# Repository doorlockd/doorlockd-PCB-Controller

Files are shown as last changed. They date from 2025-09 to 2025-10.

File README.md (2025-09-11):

# Doorlockd controller
This repository contains a PCB for a doorlockd controller, which
(together with a remote card reader) reads RFID tags and controls a lock
solenoid or other devices.

The main controller can be a Rock Pi S or Milk-V Duo S Linux board, which is
stacked on top of this PCB. This PCB then provides power, a bunch of I/O
options (for buttons, leds, RFID reader, solenoids, etc.) plus a bit of
stripboard for custom additions.

This PCB is designed to be used with other [doorlockd hardware and
software](https://github.com/doorlockd/), but can also be used with any
other software running on the same Linux boards.

See the [doorlockd organization page](https://github.com/doorlockd/) for
some info about the system in practice.

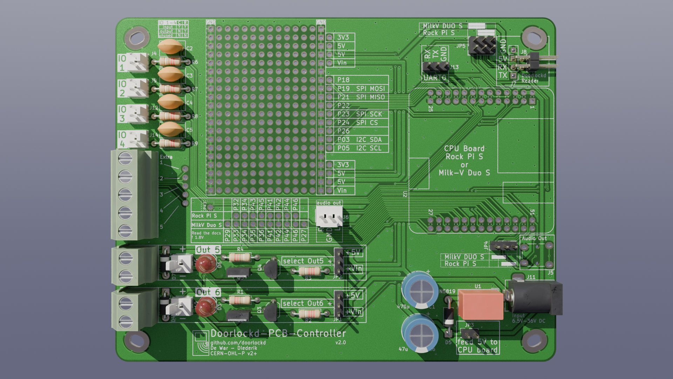
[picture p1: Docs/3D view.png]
3D rendering of PCB


## Features

This PCB provides:

 - Support for a Rock Pi S or Milk-V Duo board. To support both, in
   addition to software chagnes, some jumpers must be set correctly, and
   on there are some differences between both board for the pins on the
   stripboard area.
 - 6.5-36VDC power input (VIN), regulated to 5V to power the Linux board. 3V3
   then taken from the Linux board.
 - 4 Generic I/O circuits (numbered IO1-IO4), can be configured (by
   soldering) as direct input/output, output with series resistance or
   input with RC filter.  Available on 2.54mm pin headers directly, or
   up to 5 pins on screw terminals via wire bridges.
 - 2 low-side switched FET outputs (numbered OUT5 and OUT6) for solenoid
   or other high-current loads on screw terminals (high-side pin
   selectable between 5V and VIN).
 - UART connection to the RFID reader (e.g.
   [doorlockd-PCB-Reader](/doorlockd/doorlockd-PCB-Reader)), available
   on a square (2x2) or rectangular (1x4) connector with standard 2.54mm
   pitch. The square connector makes it easy to feed the cable through
   a round hole in e.g. a door frame.
 - 4-pin 2.54mm connector for UART connection to . Available as 1x4 pin, or
   2x2 pin (for easier feeding through a circular hole).
 - Audio (line out) on 3.5mm jack or pin header (direct from Linux
   board).
 - Stripboard area for custom extra peripherals.

## Pinout
Because the board supports two different linux board, the actual pinout
differs based on the board used.

The pins near the stripboard are intended for future experiments. The
pins to the right of the stripboard are either generic GPIO pins, or
dedicated function (SPI and I²C) pins that have the same function both
boards. All these pins support 3.3V (except for P26, which an 1.8V ADC
pin on the Rock Pi).

The pins below the stripboard are divided into a separate header for
each of the boards, since what is an IO pin on one board could be a GND
or some other special-function pin on the other. The Milk-V pins below
the stripboard only support up to 1.8V (see below).

The spreadsheet in this repository gives an overview of all pins
available on the board, where they are connected on both types of
board and what pin functions are available on those pins.

In the spreadsheet, the "doorlockd-PCB-Controller" is the main sheet to
use. This lists all the pins on the controller PCB, along with the pin
on U2 (Rock pi S or Milk-V Duo S) that it is connected to. To the right
there are two sections, one for each board, showing the name that the
board gives to that pin, and the available pin functions.

For the pin functions, three columns are available. The first column
shows a filter expression, such as `*GPIO*` and the second column shows
all pin functions (on that pin) that match the filter. The third column
is similar, except that the filter is taken from the column header (so
you can filter all pins at the same time to find a particular pin
function). You can use the `*` filter to list all available pin
functions.

The other sheets in the spreadsheet file provide are similar, but
start from the pins on the Milk-V and Rock Pi boards, instead of the
doorlockd controller PCB.

### Board selection jumpers
Some fixed-function pins (audio and card reader UART) are not (all)
available on the same place on both boards. For this reason jumpers JP4
and JP5 must be configured for the board used. If the jumpers are wrong,
the card reader RX and TX will be swapped, and the audio left channel
will be connected to 5V or a mic input channel.

### 3.3V and 1.8V pins
On the Rock Pi S all pins (except ADC) operate at 3.3V, but the Milk-V
Duo S has both 3.3V and 1.8V pins, so care should be taken when using
those pins. These 1.8V pins are used on the high-current FET inputs
(where they are shielded from the outside worled) and available on the
stripboard (on J18), where care should be taken to not overload them.

If a Milk-V Duo is used and the 3.3V pins on J22 are not sufficient, the
1.8V pins on J18 can be used. If 3.3V operation is needed, the board is
designed so a standard level shifter board can be connected with the low
side plugging into J18 and the high side into stripboard pins.

For example, using [this 8-channel shifter from
Adafruit](https://www.adafruit.com/product/395), using J18-1 (P29) as
VCCA and J18-10 (P27) as OE (configuring P29 as output high and P27 as
output low). Pin P43 is available nearby to be used for VCCB. Similarly,
[this 4-channel shfiter](https://www.adafruit.com/product/1875) can also
be used.

### ADC pins
On both boards, once ADC pin is available.

Rock pi has P26, located to the right of the stripboard. This pin is not
usable as a GPIO.

Milk-V has P46, located below the stripboard. This pin can also be used
as a GPIO.

On both boards, the ADC pins support up to 1.8V only.

## Housing
PCB dimensions: 132×103mm

The PCB has oval mounting holes supporting two different housing series:

 - RND455 121×171mm, with mounting holes spaced 118×91mm.
   This series includes: RND 455-01088 (dark grey ABS, IP67), RND
   455-01072 (light grey polycarbonate with clear lid, IP67), RND
   455-00242 (light grey polycarbonate with clear lid, IP65), 

 - RP1235 165×125mm, with mounting holes spaced 120×90mm.
   This series includes: RP1235BF (light grey ABS), RP1235BFC (light
   grey ABS with clear lid), RP1230BF (light grey polycarbonate),
   RP1230BFC (light grey polycarbonate with clear lid). Also
   RP1235/RP1235C/RP1230/RP1230C are the same but without the bottom
   flange for wall mounting. All are IP65.

The RND series is a lot cheapter, but not as widely available as the
Hammond ones.

## Origins & grid
The origins in the PCB layout became a bit inconsistent. The aux/drill
origin is set to the top left corner of the PCB (so you can set the
KiCad Display origin to drill in the KiCad preferences to get
board-local coordinates).

The grid origin was originally intended to be in the center of the
board, but with some board resizing it got misplaced. To not mess up
existing grid-aligned objects, it was left in place.

The idea was to put all connectors on a 100mil grid (to allow adding
another bit of stripboard on top and connect it to the connectors if
needed), and then components on a 20mil grid, but this was not
consistently done (so different parts of the PCB are unaligned with each
other. Oh well.

## License
Copyright 2025 Diederik Hamelink (wie-niet)
Copyright 2025 Matthijs Kooijman (matthijs@stdin.nl)

This source describes Open Hardware and is licensed under the CERN-OHL-P
v2 or any later version.

You may redistribute and modify this documentation and make products
using it under the terms of the CERN-OHL-P v2 (https:/cern.ch/cern-ohl).

This documentation is distributed WITHOUT ANY EXPRESS OR IMPLIED
WARRANTY, INCLUDING OF MERCHANTABILITY, SATISFACTORY QUALITY AND FITNESS
FOR A PARTICULAR PURPOSE. Please see the CERN-OHL-P v2 for applicable
conditions

See LICENSE.txt for the full license text.

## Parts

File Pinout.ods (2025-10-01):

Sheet: doorlockd-PCB-Controller
 |  |  | Duo S |  |  |  | Rock Pi S
 | PCB Label | U2 Pin | Name | Filter | Filter result | *FILTER* | Name (Func1) | Filter | Filter result | *FILTER*
Connectors
 | IO 1 | 16 | A20 | *GPIO* | XGPIOA[20] |  | GPIO2_B2 | *GPIO* | GPIO2_B2
 | IO 2 | 13 | B12 | *GPIO* | XGPIOB[12] (default) |  | GPIO0_C0 | *GPIO* | GPIO0_C0
 | IO 3 | 11 | B11 | *GPIO* | XGPIOB[11] (default) |  | GPIO0_B7 | *GPIO* | GPIO0_B7
 | IO 4 | 7 | B18 | *GPIO* | XGPIOB[18] (default) |  | GPIO2_A4 | *GPIO* | GPIO2_A4
 | OUT 5 | 28 | C15 | *GPIO* | XGPIOC[15] (default) |  | GPIO2_B5 | *GPIO* | GPIO2_B5
 | OUT 6 | 30 | C14 | *GPIO* | XGPIOC[14] (default) |  | GPIO2_B6 | *GPIO* | GPIO2_B6
Stripboard right
 | P18 | 18 | A19 | *GPIO* | XGPIOA[19] |  | GPIO2_B1 | *GPIO* | GPIO2_B1
 | P19 SPI MOSI | 19 | B13 | *SDO* | SPI3_SDO |  | GPIO1_C7 | *MOSI* | SPI2_MOSI
 | P21 SPI MISO | 21 | B14 | *SDI* | SPI3_SDI |  | GPIO1_C6 | *MISO* | SPI2_MISO
 | P22 | 22 | A18 | *GPIO* | XGPIOA[18] |  | GPIO2_A7 | *GPIO* | GPIO2_A7
 | P23 SPI SCK | 23 | B15 | *SCK* | SPI3_SCK |  | GPIO1_D0 | *SCK*
 | P24 SPI CS | 24 | B16 | *GPIO* | XGPIOB[16] (default) |  | GPIO1_D1 | *GPIO* | GPIO1_D1
 | P26 | 26 | A28 | *GPIO* | XGPIOA[28] |  | ADC_IN0 | *ADC* | ADC_IN0
 | P03 I2C SDA | 3 | B20 | IIC3* | IIC3_SDA |  | GPIO0_B3 | *SDA* | I2C1_SDA
 | P05 I2C SCL | 5 | B21 | IIC3* | IIC3_SCL |  | GPIO0_B4 | *SCL* | I2C1_SCL
Stripboard Rock pi s only
 | P32 | 32 | GND |  |  |  | GPIO2_B7 | *GPIO* | GPIO2_B7
 | P34 | 34 | C21 |  |  |  | GPIO2_C0 | *GPIO* | GPIO2_C0
 | P43 | 43 | 3V3 |  |  |  | GPIO2_B4 | *GPIO* | GPIO2_B4
 | P45 | 45 | AUDIO_IN_L |  |  |  | GPIO2_B0 | *GPIO* | GPIO2_B0
 | P41 | 41 | C18 |  |  |  | GPIO3_B3 | *GPIO* | GPIO3_B3
 | P42 | 42 | E1 |  |  |  | GPIO3_B2 | *GPIO* | GPIO3_B2
 | P44 | 44 | E2 |  |  |  | GPIO2_B3 | *GPIO* | GPIO2_B3
 | P46 | 46 | B3 |  |  |  | GPIO2_A6 | *GPIO* | GPIO2_A6
Stripboard Milk-V duo only (1.8V!)
 | P29 | 29 | C12 | *GPIO* | XGPIOC[12] (default) |  | ADC_KEY_IN1
 | P33 | 33 | C17 | *GPIO* | XGPIOC[17] (default) |  | MICBIAS1
 | P34 | 34 | C21 | *GPIO* | XGPIOC[21] (default) |  | GPIO2_C0
 | P35 | 35 | C16 | *GPIO* | XGPIOC[16] (default) |  | MICN8
 | P36 | 36 | C20 | *GPIO* | XGPIOC[20] (default) |  | MCIP8
 | P41 | 41 | C18 | *GPIO* | XGPIOC[18] (default) |  | GPIO3_B3
 | P42 | 42 | E1 | *GPIO* | PWR_GPIO[1] (default) |  | GPIO3_B2
 | P44 | 44 | E2 | *GPIO* | PWR_GPIO[2] (default) |  | GPIO2_B3
 | P46 | 46 | B3 | *GPIO* | XGPIOB[3] (default) |  | GPIO2_A6
 | P27 | 27 | C13 | *GPIO* | XGPIOC[13] (default) |  | GND
 | P43 | 43 | 3V3 |  |  |  | GPIO2_B4
Audio out
 | R | 51 | AUDIO_OUT_R | *AUDIO* |  |  | LINEOUT_R | *AUDIO*
 | L – Milk-V | 49 | AUDIO_OUT_L | *AUDIO* |  |  | MICN1
 | L – Rock Pi S | 52 | VSYS(5V) |  |  |  | LINEOUT_L | *AUDIO*
Card reader
 | RX – Milk-V | 15 | B22 | *UART* | UART2_RX |  | GPIO0_C1
 | RX – Rock Pi S | 40 | E0 |  |  |  | GPIO3_B4 | *UART* | UART3_RX
 | TX – Milk-V | 12 | B19 | *UART* | UART2_TX |  | GPIO2_A5
 | TX – Rock Pi S | 39 | C19 |  |  |  | GPIO3_B5 | *UART* | UART3_TX
UART0
 | RX | 10 | A17 | *UART0* | UART0_RX (default) |  | GPIO2_A0 | *UART0* | UART0_RX
 | TX | 8 | A16 | *UART0* | UART0_TX (default) |  | GPIO2_A1 | *UART0* | UART0_TX

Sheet: Combined pinout
 | Use for |  | Duo S |  |  |  | Rock Pi S
Pin | Milk V Duo S | Rock Pi S | Name | Filter | Filter result | *ADC* | Name (Func1) | Filter | Filter result | *ADC*
1 | 3V3 (Not connected) |  | 3V3 |  |  |  | +3.3V
2 | 5V |  | VSYS(5V) |  |  |  | +5.0V
3 | Exp – I2C_SDA |  | B20 | IIC3* | IIC3_SDA |  | GPIO0_B3 | I2C1* | I2C1_SDA
4 | 5V |  | VSYS(5V) |  |  |  | +5.0V
5 | Exp – I2C_SCL |  | B21 | IIC3* | IIC3_SCL |  | GPIO0_B4 | I2C1* | I2C1_SCL
6 | GND |  | GND |  |  |  | GND
7 | I/O 4 |  | B18 | *GPIO* | XGPIOB[18] (default) |  | GPIO2_A4 | *GPIO* | GPIO2_A4
8 | UART0 (console) |  | A16 | UART0* | UART0_TX (default) |  | GPIO2_A1 | UART0* | UART0_TX
9 | GND |  | GND* |  |  |  | GND
10 | UART0 (console) |  | A17 | UART0* | UART0_RX (default) |  | GPIO2_A0 | UART0* | UART0_RX
11 | I/O 3 |  | B11 | *GPIO* | XGPIOB[11] (default) |  | GPIO0_B7 | *GPIO* | GPIO0_B7
12 | PN532 (UART2_TX) | GPIO2_A5 | B19 | UART2* | UART2_TX |  | GPIO2_A5
13 | I/O 2 |  | B12 | *GPIO* | XGPIOB[12] (default) |  | GPIO0_C0 | *GPIO* | GPIO0_C0
14 | GND |  | GND |  |  |  | GND
15 | PN532 (UART2_RX) | GPIO0_C1 | B22 | UART2* | UART2_RX |  | GPIO0_C1 | *GPIO* | GPIO0_C1
16 | I/O 1 |  | A20 | *GPIO* | XGPIOA[20] |  | GPIO2_B2
17 | 3V3 |  | 3V3 |  |  |  | +3.3V
18 | Exp – UART1 | Exp – GPIO | A19 | *UART* | UART1_RTS , UART1_TX |  | GPIO2_B1 | *U*
19 | Exp – SPI |  | B13 | SPI3* | SPI3_SDO |  | GPIO1_C7 | SPI2* | SPI2_MOSI
20 | GND |  | GND |  |  |  | GND
21 | Exp – SPI |  | B14 | SPI3* | SPI3_SDI |  | GPIO1_C6 | SPI2* | SPI2_MISO
22 | Exp – UART1 | Exp – GPIO | A18 | *UART* | UART1_CTS , UART1_RX |  | GPIO2_A7
23 | Exp – SPI | Exp – SPI/UART1 | B15 | SPI3* | SPI3_SCK |  | GPIO1_D0 | UART* | UART1_RX
24 | Exp – | Exp – UART1 | B16 | * | VI2_D[5] , VI1_D[5] , VO_D[18] , XGPIOB[16] (default), RMII0_RXD0 , SPI3_CS_X , UART2_RX , CAM_HS0 |  | GPIO1_D1 | UART* | UART1_TX
25 | GND |  | GND |  |  |  | GND
26 | Exp – | Exp – ADC | A28 | *UART* | UART1_TX , UART2_TX |  | ADC_IN0 |  |  | ADC_IN0
27 | OE - XGPIOC[13] | GND | C13 | *GPIO* | XGPIOC[13] (default) |  | GND
28 | OUT_6 (5V/Vin) | 5V/Vin IO 1 – GPIO2_B5 | C15 | *GPIO* | XGPIOC[15] (default) |  | GPIO2_B5 | *GPIO* | GPIO2_B5
29 | (1.8V – XGPIOC[12] | ADC_KEY_IN | C12 | *GPIO* | XGPIOC[12] (default) |  | ADC_KEY_IN1 |  |  | ADC_KEY_IN1
30 | OUT_5 (5V/Vin) | 5V/Vin IO 1 – GPIO2_B5 | C14 | *GPIO* | XGPIOC[14] (default) |  | GPIO2_B6 | *GPIO* | GPIO2_B6
31 | NC |  | GND |  |  |  | MICBIAS2
32 | GND | GPIO2_B7 | GND | *GPIO* |  |  | GPIO2_B7 | *GPIO* | GPIO2_B7
33 | XGPIOC[17] |  | C17 | *GPIO* | XGPIOC[17] (default) |  | MICBIAS1
34 | XGPIOC[21] | GPIO2_C0 | C21 | *GPIO* | XGPIOC[21] (default) |  | GPIO2_C0 | *GPIO* | GPIO2_C0
35 | XGPIOC[16] | MICN8 | C16 | *GPIO* | XGPIOC[16] (default) |  | MICN8
36 | XGPIOC[20] | MCIP8 | C20 | *GPIO* | XGPIOC[20] (default) |  | MCIP8
37 | NC |  | GND |  |  |  | MICN7
38 | NC |  | GND |  |  |  | MCIP7
39 | XGPIOC[19] | PN532 (UART3_TX) | C19 |  |  |  | GPIO3_B5 | UART3* | UART3_TX
40 | PWR_GPIO[0] | PN532 (UART3_RX) | E0 |  |  |  | GPIO3_B4 | UART3* | UART3_RX
41 | XGPIOC[18] | GPOI3_B3 | C18 | *GPIO* | XGPIOC[18] (default) |  | GPIO3_B3 | *GP* | GPIO3_B3
42 | PWR_GPIO[1] | GPOI3_B2 | E1 | *GPIO* | PWR_GPIO[1] (default) |  | GPIO3_B2 | *GP* | GPIO3_B2
43 | 3V3 (level shifter VCCB) | GPIO2_B4 | 3V3 |  |  |  | GPIO2_B4 | *GPIO* | GPIO2_B4
44 | PWR_GPIO[2] | GPIO2_B3 | E2 | *GPIO* | PWR_GPIO[2] (default) |  | GPIO2_B3 | *GPIO* | GPIO2_B3
45 | AUDIO_IN_L | GPIO2_B0 | AUDIO_IN_L |  |  |  | GPIO2_B0 | *GPIO* | GPIO2_B0
46 | XGPIOB[3] | GPIO2_A6 | B3 | *GPIO* | XGPIOB[3] (default) |  | GPIO2_A6 | *GPIO* | GPIO2_A6
47 | NC |  | AUDIO_IN_R |  |  |  | MICN2
48 | NC |  | B2 |  |  |  | MICP2
49 | Audio L | NC | AUDIO_OUT_L | *AUDIO* |  |  | MICN1
50 | NC |  | B1 |  |  |  | MICP1
51 | Audio R | Audio R | AUDIO_OUT_R | *AUDIO* |  |  | LINEOUT_R | *OUT* | LINEOUT_R
52 | NC | Audio L | VSYS(5V) |  |  |  | LINEOUT_L | *OUT* | LINEOUT_L
NOTE: Pin 27+ on Duo S are 1.8V
NOTE: I2C2 on Duo S is also muxed to the CSI connector

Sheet: Milk-V Duo S pinout
Duo S Num | Duo S Name | SG2000 GPIO | SG2000 Pin Name | MUX filter | Filter result | UART* | SG2000 MUX 0 | SG2000 MUX 1 | SG2000 MUX 2 | SG2000 MUX 3 | SG2000 MUX 4 | SG2000 MUX 5 | SG2000 MUX 6 | SG2000 MUX 7
1 | 3V3
2 | VSYS(5V)

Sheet: Rock Pi S pinout
Rock Pi S Num | Func1 | Func2 | Func3 | Func4
1 | +3.3V
2 | +5.0V

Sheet: SG2000 Mux
Table copied from https://github.com/sophgo/sophgo-hardware/blob/master/SG200X/03_SG2000/04_SG2000_PINOUT.xlsx
Pin Num | Pin Name | IO Type | IOGroup | PowerDomain | IO_cfg_register | Function_select _register | fmux_ default | Description | Note
C4 | CAM_MCLK0 | 1.8V GPIO | G11 | VDD18A_MIPI | IOBLK_G11_REG_CAM_MCLK0 0x0300_1B00 | FMUX_GPIO_REG_IOCTRL_CAM_MCLK0 0x0300_1000 | 0x3 | IO CAM_MCLK0 function select : 0 : CAM_MCLK0 2 : AUX1 3 : XGPIOA[0] (default) Others : Reserved
C3 | CAM_PD0 | 1.8V GPIO | G11 | VDD18A_MIPI | IOBLK_G11_REG_CAM_PD0 0x0300_1B04 | FMUX_GPIO_REG_IOCTRL_CAM_PD0 0x0300_1004 | 0x3 | IO CAM_PD0 function select : 1 : IIS1_MCLK 3 : XGPIOA[1] (default) 4 : CAM_HS0 Others : Reserved
E5 | CAM_RST0 | 1.8V GPIO | G11 | VDD18A_MIPI | IOBLK_G11_REG_CAM_RST0 0x0300_1B08 | FMUX_GPIO_REG_IOCTRL_CAM_RST0 0x0300_1008 | 0x3 | IO CAM_RST0 function select : 3 : XGPIOA[2] (default) 4 : CAM_VS0 6 : IIC4_SCL Others : Reserved
D3 | CAM_MCLK1 | 1.8V GPIO | G11 | VDD18A_MIPI | IOBLK_G11_REG_CAM_MCLK1 0x0300_1B0C | FMUX_GPIO_REG_IOCTRL_CAM_MCLK1 0x0300_100C | 0x3 | IO CAM_MCLK1 function select : 0 : CAM_MCLK1 2 : AUX2 3 : XGPIOA[3] (default) 4 : CAM_HS0 Others : Reserved
E4 | CAM_PD1 | 1.8V GPIO | G11 | VDD18A_MIPI | IOBLK_G11_REG_CAM_PD1 0x0300_1B10 | FMUX_GPIO_REG_IOCTRL_CAM_PD1 0x0300_1010 | 0x3 | IO CAM_PD1 function select : 1 : IIS1_MCLK 3 : XGPIOA[4] (default) 4 : CAM_VS0 6 : IIC4_SDA Others : Reserved
D4 | IIC3_SCL | 1.8V GPIO | G11 | VDD18A_MIPI | IOBLK_G11_REG_IIC3_SCL 0x0300_1B14 | FMUX_GPIO_REG_IOCTRL_IIC3_SCL 0x0300_1014 | 0x3 | IO IIC3_SCL function select : 0 : IIC3_SCL 3 : XGPIOA[5] (default) Others : Reserved
F4 | IIC3_SDA | 1.8V GPIO | G11 | VDD18A_MIPI | IOBLK_G11_REG_IIC3_SDA 0x0300_1B18 | FMUX_GPIO_REG_IOCTRL_IIC3_SDA 0x0300_1018 | 0x3 | IO IIC3_SDA function select : 0 : IIC3_SDA 3 : XGPIOA[6] (default) Others : Reserved
L1 | SD0_CLK | 18OD33 IO | G10 | VDDIO_SD0 | IOBLK_G10_REG_SD0_CLK 0x0300_1A00 | FMUX_GPIO_REG_IOCTRL_SD0_CLK 0x0300_101C | 0x0 | IO SD0_CLK function select : 0 : SDIO0_CLK (default) 1 : IIC1_SDA 2 : SPI0_SCK 3 : XGPIOA[7] 5 : PWM[15] 6 : EPHY_LNK_LED 7 : DBG[0] Others : Reserved
L3 | SD0_CMD | 18OD33 IO | G10 | VDDIO_SD0 | IOBLK_G10_REG_SD0_CMD 0x0300_1A04 | FMUX_GPIO_REG_IOCTRL_SD0_CMD 0x0300_1020 | 0x0 | IO SD0_CMD function select : 0 : SDIO0_CMD (default) 1 : IIC1_SCL 2 : SPI0_SDO 3 : XGPIOA[8] 5 : PWM[14] 6 : EPHY_SPD_LED 7 : DBG[1] Others : Reserved
L2 | SD0_D0 | 18OD33 IO | G10 | VDDIO_SD0 | IOBLK_G10_REG_SD0_D0 0x0300_1A08 | FMUX_GPIO_REG_IOCTRL_SD0_D0 0x0300_1024 | 0x0 | IO SD0_D0 function select : 0 : SDIO0_D[0] (default) 1 : CAM_MCLK1 2 : SPI0_SDI 3 : XGPIOA[9] 4 : UART3_TX 5 : PWM[13] 6 : WG0_D0 7 : DBG[2] Others : Reserved
K3 | SD0_D1 | 18OD33 IO | G10 | VDDIO_SD0 | IOBLK_G10_REG_SD0_D1 0x0300_1A0C | FMUX_GPIO_REG_IOCTRL_SD0_D1 0x0300_1028 | 0x0 | IO SD0_D1 function select : 0 : SDIO0_D[1] (default) 1 : IIC1_SDA 2 : AUX0 3 : XGPIOA[10] 4 : UART1_TX 5 : PWM[12] 6 : WG0_D1 7 : DBG[3] Others : Reserved
M2 | SD0_D2 | 18OD33 IO | G10 | VDDIO_SD0 | IOBLK_G10_REG_SD0_D2 0x0300_1A10 | FMUX_GPIO_REG_IOCTRL_SD0_D2 0x0300_102C | 0x0 | IO SD0_D2 function select : 0 : SDIO0_D[2] (default) 1 : IIC1_SCL 2 : AUX1 3 : XGPIOA[11] 4 : UART1_RX 5 : PWM[11] 6 : WG1_D0 7 : DBG[4] Others : Reserved
M1 | SD0_D3 | 18OD33 IO | G10 | VDDIO_SD0 | IOBLK_G10_REG_SD0_D3 0x0300_1A14 | FMUX_GPIO_REG_IOCTRL_SD0_D3 0x0300_1030 | 0x0 | IO SD0_D3 function select : 0 : SDIO0_D[3] (default) 1 : CAM_MCLK0 2 : SPI0_CS_X 3 : XGPIOA[12] 4 : UART3_RX 5 : PWM[10] 6 : WG1_D1 7 : DBG[5] Others : Reserved
K2 | SD0_CD | 18OD33 IO | G7 | VDDIO_EMMC | IOBLK_G7_REG_SD0_CD 0x0300_1900 | FMUX_GPIO_REG_IOCTRL_SD0_CD 0x0300_1034 | 0x0 | IO SD0_CD function select : 0 : SDIO0_CD (default) 3 : XGPIOA[13] Others : Reserved
N1 | SD0_PWR_EN | 18OD33 IO | G7 | VDDIO_EMMC | IOBLK_G7_REG_SD0_PWR_EN 0x0300_1904 | FMUX_GPIO_REG_IOCTRL_SD0_PWR_EN 0x0300_1038 | 0x3 | IO SD0_PWR_EN function select : 0 : SDIO0_PWR_EN 3 : XGPIOA[14] (default) Others : Reserved
N3 | SPK_EN | 18OD33 IO | G7 | VDDIO_EMMC | IOBLK_G7_REG_SPK_EN 0x0300_1908 | FMUX_GPIO_REG_IOCTRL_SPK_EN 0x0300_103C | 0x3 | IO SPK_EN function select : 3 : XGPIOA[15] (default) Others : Reserved
M5 | UART0_TX | 18OD33 IO | G7 | VDDIO_EMMC | IOBLK_G7_REG_UART0_TX 0x0300_190C | FMUX_GPIO_REG_IOCTRL_UART0_TX 0x0300_1040 | 0x0 | IO UART0_TX function select : 0 : UART0_TX (default) 1 : CAM_MCLK1 2 : PWM[4] 3 : XGPIOA[16] 4 : UART1_TX 5 : AUX1 7 : DBG[6] Others : Reserved
M4 | UART0_RX | 18OD33 IO | G7 | VDDIO_EMMC | IOBLK_G7_REG_UART0_RX 0x0300_1910 | FMUX_GPIO_REG_IOCTRL_UART0_RX 0x0300_1044 | 0x0 | IO UART0_RX function select : 0 : UART0_RX (default) 1 : CAM_MCLK0 2 : PWM[5] 3 : XGPIOA[17] 4 : UART1_RX 5 : AUX0 7 : DBG[7] Others : Reserved
P4 | EMMC_RSTN | 18OD33 IO | G7 | VDDIO_EMMC | IOBLK_G7_REG_EMMC_RSTN 0x0300_1914 | FMUX_GPIO_REG_IOCTRL_EMMC_RSTN 0x0300_1048 | 0x0 | IO EMMC_RSTN function select : 0 : EMMC_RSTN (default) 3 : XGPIOA[21] 4 : AUX2 Others : Reserved
P3 | EMMC_DAT2 | 18OD33 IO | G7 | VDDIO_EMMC | IOBLK_G7_REG_EMMC_DAT2 0x0300_1918 | FMUX_GPIO_REG_IOCTRL_EMMC_DAT2 0x0300_104C | 0x1 | IO EMMC_DAT2 function select : 0 : EMMC_DAT[2] 1 : SPINOR_HOLD_X (default) 2 : SPINAND_HOLD 3 : XGPIOA[26] Others : Reserved
R4 | EMMC_CLK | 18OD33 IO | G7 | VDDIO_EMMC | IOBLK_G7_REG_EMMC_CLK 0x0300_191C | FMUX_GPIO_REG_IOCTRL_EMMC_CLK 0x0300_1050 | 0x1 | IO EMMC_CLK function select : 0 : EMMC_CLK 1 : SPINOR_SCK (default) 2 : SPINAND_CLK 3 : XGPIOA[22] Others : Reserved
P2 | EMMC_DAT0 | 18OD33 IO | G7 | VDDIO_EMMC | IOBLK_G7_REG_EMMC_DAT0 0x0300_1920 | FMUX_GPIO_REG_IOCTRL_EMMC_DAT0 0x0300_1054 | 0x1 | IO EMMC_DAT0 function select : 0 : EMMC_DAT[0] 1 : SPINOR_MOSI (default) 2 : SPINAND_MOSI 3 : XGPIOA[25] Others : Reserved
P1 | EMMC_DAT3 | 18OD33 IO | G7 | VDDIO_EMMC | IOBLK_G7_REG_EMMC_DAT3 0x0300_1924 | FMUX_GPIO_REG_IOCTRL_EMMC_DAT3 0x0300_1058 | 0x1 | IO EMMC_DAT3 function select : 0 : EMMC_DAT[3] 1 : SPINOR_WP_X (default) 2 : SPINAND_WP 3 : XGPIOA[27] Others : Reserved
R3 | EMMC_CMD | 18OD33 IO | G7 | VDDIO_EMMC | IOBLK_G7_REG_EMMC_CMD 0x0300_1928 | FMUX_GPIO_REG_IOCTRL_EMMC_CMD 0x0300_105C | 0x1 | IO EMMC_CMD function select : 0 : EMMC_CMD 1 : SPINOR_MISO (default) 2 : SPINAND_MISO 3 : XGPIOA[23] Others : Reserved
R2 | EMMC_DAT1 | 18OD33 IO | G7 | VDDIO_EMMC | IOBLK_G7_REG_EMMC_DAT1 0x0300_192C | FMUX_GPIO_REG_IOCTRL_EMMC_DAT1 0x0300_1060 | 0x1 | IO EMMC_DAT1 function select : 0 : EMMC_DAT[1] 1 : SPINOR_CS_X (default) 2 : SPINAND_CS 3 : XGPIOA[24] Others : Reserved
N6 | JTAG_CPU_TMS | 18OD33 IO | G7 | VDDIO_EMMC | IOBLK_G7_REG_JTAG_CPU_TMS 0x0300_1930 | FMUX_GPIO_REG_IOCTRL_JTAG_CPU_TMS 0x0300_1064 | 0x0 | IO JTAG_CPU_TMS function select : 0 : CR_4WTMS (default) 1 : CAM_MCLK0 2 : PWM[7] 3 : XGPIOA[19] 4 : UART1_RTS 5 : AUX0 6 : UART1_TX 7 : VO_D[28] Others : Reserved
N4 | JTAG_CPU_TCK | 18OD33 IO | G7 | VDDIO_EMMC | IOBLK_G7_REG_JTAG_CPU_TCK 0x0300_1934 | FMUX_GPIO_REG_IOCTRL_JTAG_CPU_TCK 0x0300_1068 | 0x0 | IO JTAG_CPU_TCK function select : 0 : CR_4WTCK (default) 1 : CAM_MCLK1 2 : PWM[6] 3 : XGPIOA[18] 4 : UART1_CTS 5 : AUX1 6 : UART1_RX 7 : VO_D[29] Others : Reserved
M6 | JTAG_CPU_TRST | 18OD33 IO | G7 | VDDIO_EMMC | IOBLK_G7_REG_JTAG_CPU_TRST 0x0300_1938 | FMUX_GPIO_REG_IOCTRL_JTAG_CPU_TRST 0x0300_106C | 0x0 | IO JTAG_CPU_TRST function select : 0 : JTAG_CPU_TRST (default) 3 : XGPIOA[20] 6 : VO_D[30] Others : Reserved
R6 | IIC0_SCL | 18OD33 IO | G7 | VDDIO_EMMC | IOBLK_G7_REG_IIC0_SCL 0x0300_193C | FMUX_GPIO_REG_IOCTRL_IIC0_SCL 0x0300_1070 | 0x0 | IO IIC0_SCL function select : 0 : CR_4WTDI (default) 1 : UART1_TX 2 : UART2_TX 3 : XGPIOA[28] 5 : WG0_D0 7 : DBG[10] Others : Reserved
P6 | IIC0_SDA | 18OD33 IO | G7 | VDDIO_EMMC | IOBLK_G7_REG_IIC0_SDA 0x0300_1940 | FMUX_GPIO_REG_IOCTRL_IIC0_SDA 0x0300_1074 | 0x0 | IO IIC0_SDA function select : 0 : CR_4WTDO (default) 1 : UART1_RX 2 : UART2_RX 3 : XGPIOA[29] 5 : WG0_D1 6 : WG1_D0 7 : DBG[11] Others : Reserved
P5 | AUX0 | 18OD33 IO | G7 | VDDIO_EMMC | IOBLK_G7_REG_AUX0 0x0300_1944 | FMUX_GPIO_REG_IOCTRL_AUX0 0x0300_1078 | 0x3 | IO AUX0 function select : 0 : AUX0 3 : XGPIOA[30] (default) 4 : IIS1_MCLK 5 : VO_D[31] 6 : WG1_D1 7 : DBG[12] Others : Reserved
P11 | PWR_VBAT_DET | 1.8V GPIO | GRTC | VDDIO_RTC | IOBLK_GRTC_REG_PWR_VBAT_DET 0x0502_7000 | FMUX_GPIO_REG_IOCTRL_PWR_VBAT_DET 0x0300_107C | 0x0 | IO PWR_VBAT_DET function select : 0 : PWR_VBAT_DET (default) Others : Reserved
R11 | PWR_RSTN | 1.8V GPIO | GRTC | VDDIO_RTC | IOBLK_GRTC_REG_PWR_RSTN 0x0502_7004 | FMUX_GPIO_REG_IOCTRL_PWR_RSTN 0x0300_1080 | 0x0 | IO PWR_RSTN function select : 0 : PWR_RSTN (default) Others : Reserved
P12 | PWR_SEQ1 | 1.8V GPIO | GRTC | VDDIO_RTC | IOBLK_GRTC_REG_PWR_SEQ1 0x0502_7008 | FMUX_GPIO_REG_IOCTRL_PWR_SEQ1 0x0300_1084 | 0x0 | IO PWR_SEQ1 function select : 0 : PWR_SEQ1 (default) 3 : PWR_GPIO[3] Others : Reserved
R12 | PWR_SEQ2 | 1.8V GPIO | GRTC | VDDIO_RTC | IOBLK_GRTC_REG_PWR_SEQ2 0x0502_700C | FMUX_GPIO_REG_IOCTRL_PWR_SEQ2 0x0300_1088 | 0x0 | IO PWR_SEQ2 function select : 0 : PWR_SEQ2 (default) 3 : PWR_GPIO[4] Others : Reserved
P10 | PWR_SEQ3 | 1.8V GPIO | GRTC | VDDIO_RTC | IOBLK_GRTC_REG_PWR_SEQ3 0x0502_7010 | FMUX_GPIO_REG_IOCTRL_PWR_SEQ3 0x0300_108C | 0x0 | IO PWR_SEQ3 function select : 0 : PWR_SEQ3 (default) 3 : PWR_GPIO[5] Others : Reserved
N12 | PWR_WAKEUP0 | 1.8V GPIO | GRTC | VDDIO_RTC | IOBLK_GRTC_REG_PWR_WAKEUP0 0x0502_7018 | FMUX_GPIO_REG_IOCTRL_PWR_WAKEUP0 0x0300_1090 | 0x0 | IO PWR_WAKEUP0 function select : 0 : PWR_WAKEUP0 (default) 1 : PWR_IR0 2 : PWR_UART0_TX 3 : PWR_GPIO[6] 4 : UART1_TX 5 : IIC4_SCL 6 : EPHY_LNK_LED 7 : WG2_D0 Others : Reserved
N11 | PWR_WAKEUP1 | 1.8V GPIO | GRTC | VDDIO_RTC | IOBLK_GRTC_REG_PWR_WAKEUP1 0x0502_701C | FMUX_GPIO_REG_IOCTRL_PWR_WAKEUP1 0x0300_1094 | 0x0 | IO PWR_WAKEUP1 function select : 0 : PWR_WAKEUP1 (default) 1 : PWR_IR1 3 : PWR_GPIO[7] 4 : UART1_TX 5 : IIC4_SCL 6 : EPHY_LNK_LED 7 : WG0_D0 Others : Reserved
P13 | PWR_BUTTON1 | 1.8V GPIO | GRTC | VDDIO_RTC | IOBLK_GRTC_REG_PWR_BUTTON1 0x0502_7020 | FMUX_GPIO_REG_IOCTRL_PWR_BUTTON1 0x0300_1098 | 0x0 | IO PWR_BUTTON1 function select : 0 : PWR_BUTTON1 (default) 3 : PWR_GPIO[8] 4 : UART1_RX 5 : IIC4_SDA 6 : EPHY_SPD_LED 7 : WG2_D1 Others : Reserved
M11 | PWR_ON | 1.8V GPIO | GRTC | VDDIO_RTC | IOBLK_GRTC_REG_PWR_ON 0x0502_7024 | FMUX_GPIO_REG_IOCTRL_PWR_ON 0x0300_109C | 0x0 | IO PWR_ON function select : 0 : PWR_ON (default) 3 : PWR_GPIO[9] 4 : UART1_RX 5 : IIC4_SDA 6 : EPHY_SPD_LED 7 : WG0_D1 Others : Reserved
R13 | XTAL_XIN | Xtal | GRTC | VDDIO_RTC | IOBLK_GRTC_REG_XTAL_XIN 0x0502_7028 | FMUX_GPIO_REG_IOCTRL_XTAL_XIN 0x0300_10A0 | 0x0 | IO XTAL_XIN function select : 0 : PWR_XTAL_CLKIN (default) Others : Reserved
M13 | PWR_GPIO0 | 1.8V GPIO | GRTC | VDDIO_RTC | IOBLK_GRTC_REG_PWR_GPIO0 0x0502_702C | FMUX_GPIO_REG_IOCTRL_PWR_GPIO0 0x0300_10A4 | 0x0 | IO PWR_GPIO0 function select : 0 : PWR_GPIO[0] (default) 1 : UART2_TX 2 : PWR_UART0_RX 4 : PWM[8] Others : Reserved
N13 | PWR_GPIO1 | 1.8V GPIO | GRTC | VDDIO_RTC | IOBLK_GRTC_REG_PWR_GPIO1 0x0502_7030 | FMUX_GPIO_REG_IOCTRL_PWR_GPIO1 0x0300_10A8 | 0x0 | IO PWR_GPIO1 function select : 0 : PWR_GPIO[1] (default) 1 : UART2_RX 3 : EPHY_LNK_LED 4 : PWM[9] 5 : PWR_IIC_SCL 6 : IIC2_SCL 7 : CR_SDA0 Others : Reserved
M12 | PWR_GPIO2 | 1.8V GPIO | GRTC | VDDIO_RTC | IOBLK_GRTC_REG_PWR_GPIO2 0x0502_7034 | FMUX_GPIO_REG_IOCTRL_PWR_GPIO2 0x0300_10AC | 0x0 | IO PWR_GPIO2 function select : 0 : PWR_GPIO[2] (default) 2 : PWR_SECTICK 3 : EPHY_SPD_LED 4 : PWM[10] 5 : PWR_IIC_SDA 6 : IIC2_SDA 7 : CR_2WTCK Others : Reserved
L14 | CLK32K | 1.8V GPIO | GRTC | VDDIO_RTC | IOBLK_GRTC_REG_CLK32K 0x0502_7038 | FMUX_GPIO_REG_IOCTRL_CLK32K 0x0300_10B0 | 0x0 | IO CLK32K function select : 0 : CLK32K (default) 1 : AUX0 2 : CR_SCL0 3 : PWR_GPIO[10] 4 : PWM[2] 5 : KEY_COL0 6 : CAM_MCLK0 7 : DBG[0] Others : Reserved
M14 | CLK25M | 1.8V GPIO | GRTC | VDDIO_RTC | IOBLK_GRTC_REG_CLK25M 0x0502_703C | FMUX_GPIO_REG_IOCTRL_CLK25M 0x0300_10B4 | 0x0 | IO CLK25M function select : 0 : CLK25M (default) 1 : AUX1 2 : CR_2WTMS 3 : PWR_GPIO[11] 4 : PWM[3] 5 : KEY_COL1 6 : CAM_MCLK1 7 : DBG[1] Others : Reserved
J13 | IIC2_SCL | 1.8V GPIO | GRTC | VDDIO_RTC | IOBLK_GRTC_REG_IIC2_SCL 0x0502_7040 | FMUX_GPIO_REG_IOCTRL_IIC2_SCL 0x0300_10B8 | 0x3 | IO IIC2_SCL function select : 0 : IIC2_SCL 1 : PWM[14] 3 : PWR_GPIO[12] (default) 4 : UART2_RX 7 : KEY_COL2 Others : Reserved
J14 | IIC2_SDA | 1.8V GPIO | GRTC | VDDIO_RTC | IOBLK_GRTC_REG_IIC2_SDA 0x0502_7044 | FMUX_GPIO_REG_IOCTRL_IIC2_SDA 0x0300_10BC | 0x3 | IO IIC2_SDA function select : 0 : IIC2_SDA 1 : PWM[15] 3 : PWR_GPIO[13] (default) 4 : UART2_TX 5 : IIS1_MCLK 6 : IIS2_MCLK 7 : KEY_COL3 Others : Reserved
K15 | UART2_TX | 1.8V GPIO | GRTC | VDDIO_RTC | IOBLK_GRTC_REG_UART2_TX 0x0502_7048 | FMUX_GPIO_REG_IOCTRL_UART2_TX 0x0300_10C0 | 0x3 | IO UART2_TX function select : 0 : UART2_TX 1 : PWM[11] 2 : PWR_UART1_TX 3 : PWR_GPIO[14] (default) 4 : KEY_ROW3 5 : UART4_TX 6 : IIS2_BCLK 7 : WG2_D0 Others : Reserved
L15 | UART2_RTS | 1.8V GPIO | GRTC | VDDIO_RTC | IOBLK_GRTC_REG_UART2_RTS 0x0502_704C | FMUX_GPIO_REG_IOCTRL_UART2_RTS 0x0300_10C4 | 0x3 | IO UART2_RTS function select : 0 : UART2_RTS 1 : PWM[8] 3 : PWR_GPIO[15] (default) 4 : KEY_ROW0 5 : UART4_RTS 6 : IIS2_DO 7 : WG1_D0 Others : Reserved
K13 | UART2_RX | 1.8V GPIO | GRTC | VDDIO_RTC | IOBLK_GRTC_REG_UART2_RX 0x0502_7050 | FMUX_GPIO_REG_IOCTRL_UART2_RX 0x0300_10C8 | 0x3 | IO UART2_RX function select : 0 : UART2_RX 1 : PWM[10] 2 : PWR_UART1_RX 3 : PWR_GPIO[16] (default) 4 : KEY_COL3 5 : UART4_RX 6 : IIS2_DI 7 : WG2_D1 Others : Reserved
K14 | UART2_CTS | 1.8V GPIO | GRTC | VDDIO_RTC | IOBLK_GRTC_REG_UART2_CTS 0x0502_7054 | FMUX_GPIO_REG_IOCTRL_UART2_CTS 0x0300_10CC | 0x3 | IO UART2_CTS function select : 0 : UART2_CTS 1 : PWM[9] 3 : PWR_GPIO[17] (default) 4 : KEY_ROW1 5 : UART4_CTS 6 : IIS2_LRCK 7 : WG1_D1 Others : Reserved
G13 | SD1_D3 | 18OD33 IO | GRTC | VDDIO_SD1 | IOBLK_GRTC_REG_SD1_D3 0x0502_7058 | FMUX_GPIO_REG_IOCTRL_SD1_D3 0x0300_10D0 | 0x6 | IO SD1_D3 function select : 0 : PWR_SD1_D3_VO32 1 : SPI2_CS_X 2 : IIC1_SCL 3 : PWR_GPIO[18] 4 : CAM_MCLK0 5 : UART3_CTS 6 : PWR_SPINOR1_CS_X (default) 7 : PWM[4] Others : Reserved | SD1_D3 or VO[32] Check 0x0502_70E4
F14 | SD1_D2 | 18OD33 IO | GRTC | VDDIO_SD1 | IOBLK_GRTC_REG_SD1_D2 0x0502_705C | FMUX_GPIO_REG_IOCTRL_SD1_D2 0x0300_10D4 | 0x6 | IO SD1_D2 function select : 0 : PWR_SD1_D2_VO33 1 : IIC1_SCL 2 : UART2_TX 3 : PWR_GPIO[19] 4 : CAM_MCLK0 5 : UART3_TX 6 : PWR_SPINOR1_HOLD_X (default) 7 : PWM[5] Others : Reserved | SD1_D2 or VO[33] Check 0x0502_70E4
H14 | SD1_D1 | 18OD33 IO | GRTC | VDDIO_SD1 | IOBLK_GRTC_REG_SD1_D1 0x0502_7060 | FMUX_GPIO_REG_IOCTRL_SD1_D1 0x0300_10D8 | 0x6 | IO SD1_D1 function select : 0 : PWR_SD1_D1_VO34 1 : IIC1_SDA 2 : UART2_RX 3 : PWR_GPIO[20] 4 : CAM_MCLK1 5 : UART3_RX 6 : PWR_SPINOR1_WP_X (default) 7 : PWM[6] Others : Reserved | SD1_D1 or VO[34] Check 0x0502_70E4
H15 | SD1_D0 | 18OD33 IO | GRTC | VDDIO_SD1 | IOBLK_GRTC_REG_SD1_D0 0x0502_7064 | FMUX_GPIO_REG_IOCTRL_SD1_D0 0x0300_10DC | 0x6 | IO SD1_D0 function select : 0 : PWR_SD1_D0_VO35 1 : SPI2_SDI 2 : IIC1_SDA 3 : PWR_GPIO[21] 4 : CAM_MCLK1 5 : UART3_RTS 6 : PWR_SPINOR1_MISO (default) 7 : PWM[7] Others : Reserved | SD1_D0 or VO[35] Check 0x0502_70E4
G15 | SD1_CMD | 18OD33 IO | GRTC | VDDIO_SD1 | IOBLK_GRTC_REG_SD1_CMD 0x0502_7068 | FMUX_GPIO_REG_IOCTRL_SD1_CMD 0x0300_10E0 | 0x6 | IO SD1_CMD function select : 0 : PWR_SD1_CMD_VO36 1 : SPI2_SDO 2 : IIC3_SCL 3 : PWR_GPIO[22] 4 : CAM_VS0 5 : EPHY_LNK_LED 6 : PWR_SPINOR1_MOSI (default) 7 : PWM[8] Others : Reserved | SD1_CMD or VO[36] Check 0x0502_70E4
G14 | SD1_CLK | 18OD33 IO | GRTC | VDDIO_SD1 | IOBLK_GRTC_REG_SD1_CLK 0x0502_706C | FMUX_GPIO_REG_IOCTRL_SD1_CLK 0x0300_10E4 | 0x6 | IO SD1_CLK function select : 0 : PWR_SD1_CLK_VO37 1 : SPI2_SCK 2 : IIC3_SDA 3 : PWR_GPIO[23] 4 : CAM_HS0 5 : EPHY_SPD_LED 6 : PWR_SPINOR1_SCK (default) 7 : PWM[9] Others : Reserved | SD1_CLK or VO[37] Check 0x0502_70E4
H12 | RSTN | 1.8V GPIO | G1 | VDDIO18_1 | IOBLK_G1_REG_RSTN 0x0300_1800 | FMUX_GPIO_REG_IOCTRL_RSTN 0x0300_10E8 | 0x0 | IO RSTN function select : 0 : RSTN (default) Others : Reserved
H13 | PWM0_BUCK | 1.8V GPIO | G1 | VDDIO18_1 | IOBLK_G1_REG_PWM0_BUCK 0x0300_1804 | FMUX_GPIO_REG_IOCTRL_PWM0_BUCK 0x0300_10EC | 0x3 | IO PWM0_BUCK function select : 0 : PWM[0] 3 : XGPIOB[0] (default) Others : Reserved
E15 | ADC3 | 1.8V GPIO | G1 | VDDIO18_1 | IOBLK_G1_REG_ADC3 0x0300_1808 | FMUX_GPIO_REG_IOCTRL_ADC3 0x0300_10F0 | 0x3 | IO ADC3 function select : 1 : CAM_MCLK0 2 : IIC4_SCL 3 : XGPIOB[1] (default) 4 : PWM[12] 5 : EPHY_LNK_LED 6 : WG2_D0 7 : UART3_TX Others : Reserved
E14 | ADC2 | 1.8V GPIO | G1 | VDDIO18_1 | IOBLK_G1_REG_ADC2 0x0300_180C | FMUX_GPIO_REG_IOCTRL_ADC2 0x0300_10F4 | 0x3 | IO ADC2 function select : 1 : CAM_MCLK1 2 : IIC4_SDA 3 : XGPIOB[2] (default) 4 : PWM[13] 5 : EPHY_SPD_LED 6 : WG2_D1 7 : UART3_RX Others : Reserved
E13 | ADC1 | 1.8V GPIO | G1 | VDDIO18_1 | IOBLK_G1_REG_ADC1 0x0300_1810 | FMUX_GPIO_REG_IOCTRL_ADC1 0x0300_10F8 | 0x3 | IO ADC1 function select : 3 : XGPIOB[3] (default) 4 : KEY_COL2 Others : Reserved
B13 | USB_ID | 1.8V GPIO | G1 | VDDIO18_1 | IOBLK_G1_REG_USB_ID 0x0300_1814 | FMUX_GPIO_REG_IOCTRL_USB_ID 0x0300_10FC | 0x0 | IO USB_ID function select : 0 : USB_ID (default) 3 : XGPIOB[4] Others : Reserved
C12 | USB_VBUS_EN | 1.8V GPIO | G1 | VDDIO18_1 | IOBLK_G1_REG_USB_VBUS_EN 0x0300_1818 | FMUX_GPIO_REG_IOCTRL_USB_VBUS_EN 0x0300_1100 | 0x0 | IO USB_VBUS_EN function select : 0 : USB_VBUS_EN (default) 3 : XGPIOB[5] Others : Reserved
A13 | USB_VBUS_DET | 1.8V GPIO | G1 | VDDIO18_1 | IOBLK_G1_REG_USB_VBUS_DET 0x0300_1820 | FMUX_GPIO_REG_IOCTRL_USB_VBUS_DET 0x0300_1108 | 0x0 | IO USB_VBUS_DET function select : 0 : USB_VBUS_DET (default) 3 : XGPIOB[6] 4 : CAM_MCLK0 5 : CAM_MCLK1 Others : Reserved
D15 | PAD_ETH_TXP___EPHY_RXN | ETH GPIO (1.8V) |  | VDD18A_EPHY | #N/A | FMUX_GPIO_REG_IOCTRL_PAD_ETH_TXP 0x0300_1124 | 0x3 | IO PAD_ETH_TXP function select : 1 : UART3_RX 2 : IIC1_SCL 3 : XGPIOB[25] (default) 4 : PWM[13] 5 : CAM_MCLK0 6 : SPI1_SDO 7 : IIS2_LRCK Others : Reserved
D14 | PAD_ETH_TXM___EPHY_RXP | ETH GPIO (1.8V) |  | VDD18A_EPHY | #N/A | FMUX_GPIO_REG_IOCTRL_PAD_ETH_TXM 0x0300_1128 | 0x3 | IO PAD_ETH_TXM function select : 1 : UART3_RTS 2 : IIC1_SDA 3 : XGPIOB[24] (default) 4 : PWM[12] 5 : CAM_MCLK1 6 : SPI1_SDI 7 : IIS2_BCLK Others : Reserved
C14 | PAD_ETH_RXP___EPHY_TXN | ETH GPIO (1.8V) |  | VDD18A_EPHY | #N/A | FMUX_GPIO_REG_IOCTRL_PAD_ETH_RXP 0x0300_112C | 0x3 | IO PAD_ETH_RXP function select : 1 : UART3_TX 2 : CAM_MCLK1 3 : XGPIOB[27] (default) 4 : PWM[15] 5 : CAM_HS0 6 : SPI1_SCK 7 : IIS2_DO Others : Reserved
B15 | PAD_ETH_RXM___EPHY_TXP | ETH GPIO (1.8V) |  | VDD18A_EPHY | #N/A | FMUX_GPIO_REG_IOCTRL_PAD_ETH_RXM 0x0300_1130 | 0x3 | IO PAD_ETH_RXM function select : 1 : UART3_CTS 2 : CAM_MCLK0 3 : XGPIOB[26] (default) 4 : PWM[14] 5 : CAM_VS0 6 : SPI1_CS_X 7 : IIS2_DI Others : Reserved
A12 | VIVO_D10 | 18OD33 IO | G12 | VDDIO_VIVO | IOBLK_G12_REG_VIVO_D10 0x0300_1C00 | FMUX_GPIO_REG_IOCTRL_VIVO_D10 0x0300_1134 | 0x3 | IO VIVO_D10 function select : 0 : PWM[1] 1 : VI1_D[10] 2 : VO_D[23] 3 : XGPIOB[11] (default) 4 : RMII0_IRQ 5 : CAM_MCLK0 6 : IIC1_SDA 7 : UART2_TX Others : Reserved
B12 | VIVO_D9 | 18OD33 IO | G12 | VDDIO_VIVO | IOBLK_G12_REG_VIVO_D9 0x0300_1C04 | FMUX_GPIO_REG_IOCTRL_VIVO_D9 0x0300_1138 | 0x3 | IO VIVO_D9 function select : 0 : PWM[2] 1 : VI1_D[9] 2 : VO_D[22] 3 : XGPIOB[12] (default) 5 : CAM_MCLK1 6 : IIC1_SCL 7 : UART2_RX Others : Reserved
C11 | VIVO_D8 | 18OD33 IO | G12 | VDDIO_VIVO | IOBLK_G12_REG_VIVO_D8 0x0300_1C08 | FMUX_GPIO_REG_IOCTRL_VIVO_D8 0x0300_113C | 0x3 | IO VIVO_D8 function select : 0 : PWM[3] 1 : VI1_D[8] 2 : VO_D[21] 3 : XGPIOB[13] (default) 4 : RMII0_MDIO 5 : SPI3_SDO 6 : IIC2_SCL 7 : CAM_VS0 Others : Reserved
B11 | VIVO_D7 | 18OD33 IO | G12 | VDDIO_VIVO | IOBLK_G12_REG_VIVO_D7 0x0300_1C0C | FMUX_GPIO_REG_IOCTRL_VIVO_D7 0x0300_1140 | 0x3 | IO VIVO_D7 function select : 0 : VI2_D[7] 1 : VI1_D[7] 2 : VO_D[20] 3 : XGPIOB[14] (default) 4 : RMII0_RXD1 5 : SPI3_SDI 6 : IIC2_SDA 7 : CAM_HS0 Others : Reserved
C10 | VIVO_D6 | 18OD33 IO | G12 | VDDIO_VIVO | IOBLK_G12_REG_VIVO_D6 0x0300_1C10 | FMUX_GPIO_REG_IOCTRL_VIVO_D6 0x0300_1144 | 0x3 | IO VIVO_D6 function select : 0 : VI2_D[6] 1 : VI1_D[6] 2 : VO_D[19] 3 : XGPIOB[15] (default) 4 : RMII0_REFCLKI 5 : SPI3_SCK 6 : UART2_TX 7 : CAM_VS0 Others : Reserved
B10 | VIVO_D5 | 18OD33 IO | G12 | VDDIO_VIVO | IOBLK_G12_REG_VIVO_D5 0x0300_1C14 | FMUX_GPIO_REG_IOCTRL_VIVO_D5 0x0300_1148 | 0x3 | IO VIVO_D5 function select : 0 : VI2_D[5] 1 : VI1_D[5] 2 : VO_D[18] 3 : XGPIOB[16] (default) 4 : RMII0_RXD0 5 : SPI3_CS_X 6 : UART2_RX 7 : CAM_HS0 Others : Reserved
D10 | VIVO_D4 | 18OD33 IO | G12 | VDDIO_VIVO | IOBLK_G12_REG_VIVO_D4 0x0300_1C18 | FMUX_GPIO_REG_IOCTRL_VIVO_D4 0x0300_114C | 0x3 | IO VIVO_D4 function select : 0 : VI2_D[4] 1 : VI1_D[4] 2 : VO_D[17] 3 : XGPIOB[17] (default) 4 : RMII0_MDC 5 : IIC1_SDA 6 : UART2_CTS 7 : CAM_VS0 Others : Reserved
A10 | VIVO_D3 | 18OD33 IO | G12 | VDDIO_VIVO | IOBLK_G12_REG_VIVO_D3 0x0300_1C1C | FMUX_GPIO_REG_IOCTRL_VIVO_D3 0x0300_1150 | 0x3 | IO VIVO_D3 function select : 0 : VI2_D[3] 1 : VI1_D[3] 2 : VO_D[16] 3 : XGPIOB[18] (default) 4 : RMII0_TXD0 5 : IIC1_SCL 6 : UART2_RTS 7 : CAM_HS0 Others : Reserved
A9 | VIVO_D2 | 18OD33 IO | G12 | VDDIO_VIVO | IOBLK_G12_REG_VIVO_D2 0x0300_1C20 | FMUX_GPIO_REG_IOCTRL_VIVO_D2 0x0300_1154 | 0x3 | IO VIVO_D2 function select : 0 : VI2_D[2] 1 : VI1_D[2] 2 : VO_D[15] 3 : XGPIOB[19] (default) 4 : RMII0_TXD1 5 : CAM_MCLK1 6 : PWM[2] 7 : UART2_TX Others : Reserved
B9 | VIVO_D1 | 18OD33 IO | G12 | VDDIO_VIVO | IOBLK_G12_REG_VIVO_D1 0x0300_1C24 | FMUX_GPIO_REG_IOCTRL_VIVO_D1 0x0300_1158 | 0x3 | IO VIVO_D1 function select : 0 : VI2_D[1] 1 : VI1_D[1] 2 : VO_D[14] 3 : XGPIOB[20] (default) 4 : RMII0_RXDV 5 : IIC3_SDA 6 : PWM[3] 7 : IIC4_SCL Others : Reserved
E10 | VIVO_D0 | 18OD33 IO | G12 | VDDIO_VIVO | IOBLK_G12_REG_VIVO_D0 0x0300_1C28 | FMUX_GPIO_REG_IOCTRL_VIVO_D0 0x0300_115C | 0x3 | IO VIVO_D0 function select : 0 : VI2_D[0] 1 : VI1_D[0] 2 : VO_D[13] 3 : XGPIOB[21] (default) 4 : RMII0_TXCLK 5 : IIC3_SCL 6 : WG1_D0 7 : IIC4_SDA Others : Reserved
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

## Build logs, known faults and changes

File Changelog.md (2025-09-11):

Doorlockd-PCB-Controller version 2.0 components 2025-09-11
==========================================================
 - Heavily revised version of Doorlockd-PCB-BBB, modified to use Milk-V
   Duo S or Rock Pi S instead of Beaglebone Black. This version also
   adds a bit of stripboard for customizations and has a bit more
   flexible IO instead of fixed-function LED and button connectors.

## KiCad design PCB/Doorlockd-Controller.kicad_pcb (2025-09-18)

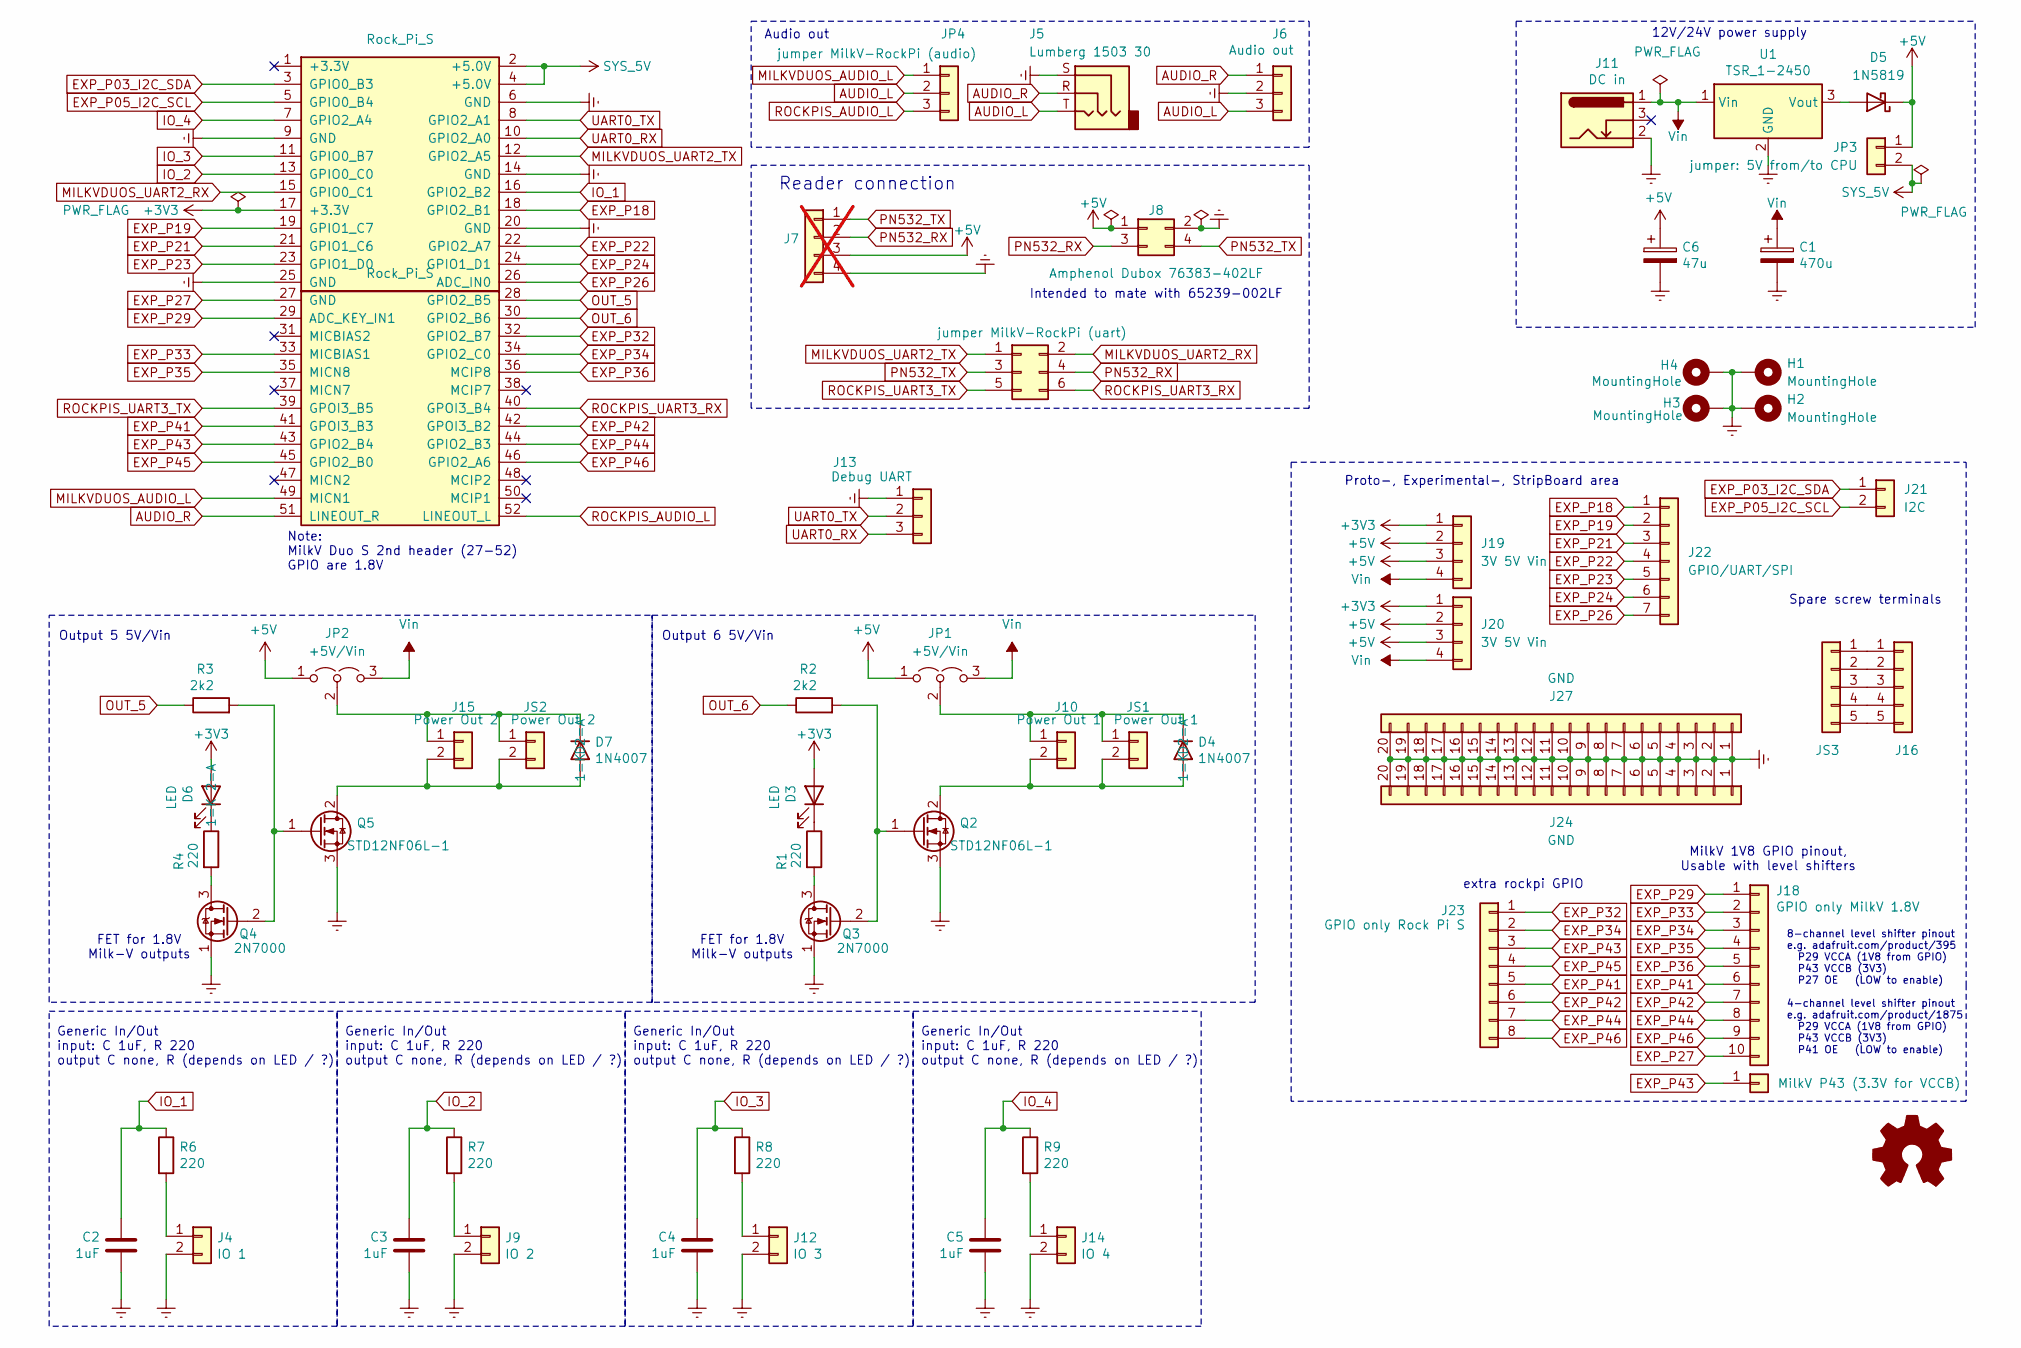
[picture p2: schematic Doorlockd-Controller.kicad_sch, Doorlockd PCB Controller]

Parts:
C1: 470u; CP_Radial_D10.0mm_P5.00mm
C2, C3, C4, C5: 1uF; C_Disc_D7.5mm_W4.4mm_P5.00mm
C6: 47u; CP_Radial_D10.0mm_P5.00mm
D3, D6: LED; LED_D5.0mm
D4, D7: 1N4007; D_DO-41_SOD81_P7.62mm_Horizontal
D5: 1N5819; D_DO-41_SOD81_P10.16mm_Horizontal
H1, H2, H3, H4: MountingHole; MountingHole_Dual_3.2mm_M3_Offset1x0.5mm
J1: MilkV P43 (3.3V for VCCB); StripBoard_1x01_P2.54mm
J4: IO 1; Molex_KK-254_AE-6410-02A_1x02_P2.54mm_Vertical
J5: Lumberg 1503 30; Jack_3.5mm_Lumberg_1503_07_Horizontal
J6: Audio out; Molex_KK-254_AE-6410-03A_1x03_P2.54mm_Vertical
J7: Conn_01x04; PinHeader_1x04_P2.54mm_Vertical; not fitted
J8: Amphenol Dubox ‎76383-402LF‎; PinHeader_2x02_P2.54mm_Horizontal
J9: IO 2; Molex_KK-254_AE-6410-02A_1x02_P2.54mm_Vertical
J10: Power Out 1; Molex_KK-254_AE-6410-02A_1x02_P2.54mm_Vertical
J11: DC in; BarrelJack_Horizontal
J12: IO 3; Molex_KK-254_AE-6410-02A_1x02_P2.54mm_Vertical
J13: Debug UART; PinHeader_1x03_P2.54mm_Vertical
J14: IO 4; Molex_KK-254_AE-6410-02A_1x02_P2.54mm_Vertical
J15: Power Out 2; Molex_KK-254_AE-6410-02A_1x02_P2.54mm_Vertical
J16: to extra screw conn.; StripBoard_1x05_P2.54mm
J18: GPIO only MilkV 1.8V; StripBoard_1x10_P2.54mm
J19, J20: 3V 5V Vin; StripBoard_1x04_P2.54mm
J21: I2C; StripBoard_1x02_P2.54mm
J22: GPIO/UART/SPI; StripBoard_1x07_P2.54mm
J23: GPIO only Rock Pi S; StripBoard_1x08_P2.54mm
J24, J27: GND; StripBoard_1x20_P2.54mm_Square
JP1, JP2: +5V/Vin; PinHeader_1x03_P2.54mm_Vertical
JP3: jumper: 5V from/to CPU; PinHeader_2x01_P2.54mm_Vertical
JP4: jumper MilkV-RockPi (audio); PinHeader_1x03_P2.54mm_Vertical
JP5: jumper MilkV-RockPi (uart); PinHeader_2x03_P2.54mm_Vertical
JS1: Power Out 1; TerminalBlock_Phoenix_MKDS-3-2-5.08_1x02_P5.08mm_Horizontal
JS2: Power Out 2; TerminalBlock_Phoenix_MKDS-3-2-5.08_1x02_P5.08mm_Horizontal
JS3: Extra Screw conn; TerminalBlock_Phoenix_MKDS-3-5-5.08_1x05_P5.08mm_Horizontal
Q2, Q5: STD12NF06L-1; TO-251-3_Vertical
Q3, Q4: 2N7000; TO-92_Wide
R1, R4, R6, R7, R8, R9: 220; R_Axial_DIN0207_L6.3mm_D2.5mm_P10.16mm_Horizontal
R2, R3: 2k2; R_Axial_DIN0207_L6.3mm_D2.5mm_P10.16mm_Horizontal
U1: TSR_1-2450; Converter_DCDC_TRACO_TSR-1_THT
U2: Rock_Pi_S

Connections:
+3V3: D3.2 (A), D6.2 (A), J19.1, J20.1, U2.17 (+3.3V)
+5V: C6.1, D5.1 (K), J7.3, J8.1, J19.2, J19.3, J20.2, J20.3, JP1.1 (A), JP2.1 (A), JP3.1
AUDIO_L: J5.T, J6.3, JP4.2
AUDIO_R: J5.R, J6.1, U2.51 (LINEOUT_R)
EXP_P03_I2C_SDA: J21.1, U2.3 (GPIO0_B3)
EXP_P05_I2C_SCL: J21.2, U2.5 (GPIO0_B4)
EXP_P18: J22.1, U2.18 (GPIO2_B1)
EXP_P19: J22.2, U2.19 (GPIO1_C7)
EXP_P21: J22.3, U2.21 (GPIO1_C6)
EXP_P22: J22.4, U2.22 (GPIO2_A7)
EXP_P23: J22.5, U2.23 (GPIO1_D0)
EXP_P24: J22.6, U2.24 (GPIO1_D1)
EXP_P26: J22.7, U2.26 (ADC_IN0)
EXP_P27: J18.10, U2.27 (GND)
EXP_P29: J18.1, U2.29 (ADC_KEY_IN1)
EXP_P32: J23.1, U2.32 (GPIO2_B7)
EXP_P33: J18.2, U2.33 (MICBIAS1)
EXP_P34: J18.3, J23.2, U2.34 (GPIO2_C0)
EXP_P35: J18.4, U2.35 (MICN8)
EXP_P36: J18.5, U2.36 (MCIP8)
EXP_P41: J18.6, J23.5, U2.41 (GPOI3_B3)
EXP_P42: J18.7, J23.6, U2.42 (GPOI3_B2)
EXP_P43: J1.1, J23.3, U2.43 (GPIO2_B4)
EXP_P44: J18.8, J23.7, U2.44 (GPIO2_B3)
EXP_P45: J23.4, U2.45 (GPIO2_B0)
EXP_P46: J18.9, J23.8, U2.46 (GPIO2_A6)
Earth: C1.2, C2.1, C3.1, C4.1, C5.1, C6.2, H1.1, H2.1, H3.1, H4.1, J4.2, J5.S, J6.2, J7.4, J8.2, J9.2, J11.2, J12.2, J13.1, J14.2, J24.1, J24.2, J24.3, J24.4, J24.5, J24.6, J24.7, J24.8, J24.9, J24.10, J24.11, J24.12, J24.13, J24.14, J24.15, J24.16, J24.17, J24.18, J24.19, J24.20, J27.1, J27.2, J27.3, J27.4, J27.5, J27.6, J27.7, J27.8, J27.9, J27.10, J27.11, J27.12, J27.13, J27.14, J27.15, J27.16, J27.17, J27.18, J27.19, J27.20, Q2.3 (S), Q3.1 (S), Q4.1 (S), Q5.3 (S), U1.2 (GND), U2.6 (GND), U2.9 (GND), U2.14 (GND), U2.20 (GND), U2.25 (GND)
IO_1: C2.2, R6.1, U2.16 (GPIO2_B2)
IO_2: C3.2, R7.1, U2.13 (GPIO0_C0)
IO_3: C4.2, R8.1, U2.11 (GPIO0_B7)
IO_4: C5.2, R9.1, U2.7 (GPIO2_A4)
MILKVDUOS_AUDIO_L: JP4.1, U2.49 (MICN1)
MILKVDUOS_UART2_RX: JP5.2, U2.15 (GPIO0_C1)
MILKVDUOS_UART2_TX: JP5.1, U2.12 (GPIO2_A5)
unnamed: D3.1 (K), R1.1
unnamed: D4.2 (A), J10.2, JS1.2, Q2.2 (D)
unnamed: D4.1 (K), J10.1, JP1.2 (C), JS1.1
unnamed: D5.2 (A), U1.3 (Vout)
unnamed: D6.1 (K), R4.1
unnamed: D7.2 (A), J15.2, JS2.2, Q5.2 (D)
unnamed: D7.1 (K), J15.1, JP2.2 (C), JS2.1
unnamed: J4.1, R6.2
unnamed: J9.1, R7.2
unnamed: J12.1, R8.2
unnamed: J14.1, R9.2
unnamed: J16.1, JS3.1
unnamed: J16.2, JS3.2
unnamed: J16.3, JS3.3
unnamed: J16.4, JS3.4
unnamed: J16.5, JS3.5
unnamed: Q2.1 (G), Q3.2 (G), R2.2
unnamed: Q3.3 (D), R1.2
unnamed: Q4.3 (D), R4.2
unnamed: Q4.2 (G), Q5.1 (G), R3.2
OUT_5: R3.1, U2.28 (GPIO2_B5)
OUT_6: R2.1, U2.30 (GPIO2_B6)
PN532_RX: J7.2, J8.3, JP5.4
PN532_TX: J7.1, J8.4, JP5.3
ROCKPIS_AUDIO_L: JP4.3, U2.52 (LINEOUT_L)
ROCKPIS_UART3_RX: JP5.6, U2.40 (GPOI3_B4)
ROCKPIS_UART3_TX: JP5.5, U2.39 (GPOI3_B5)
SYS_5V: JP3.2, U2.2 (+5.0V), U2.4 (+5.0V)
UART0_RX: J13.3, U2.10 (GPIO2_A0)
UART0_TX: J13.2, U2.8 (GPIO2_A1)
Vin: C1.1, J11.1, J19.4, J20.4, JP1.3 (B), JP2.3 (B), U1.1 (Vin)

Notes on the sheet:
Generic In/Out input: C 1uF, R 220 output C none, R (depends on LED / ?)
Reader connection
Output 5 5V/Vin
FET for 1.8V Milk-V outputs
MilkV 1V8 GPIO pinout, Usable with level shifters
Intended to mate with 65239-002LF
Spare screw terminals
Output 6 5V/Vin
8-channel level shifter pinout e.g. adafruit.com/product/395 P29 VCCA (1V8 from GPIO) P43 VCCB (3V3) P27 OE (LOW to enable) 4-channel level shifter pinout e.g. adafruit.com/product/1875 P29 VCCA (1V8 from GPIO) P43 VCCB (3V3) P41 OE (LOW to enable)
Proto-, Experimental-, StripBoard area
extra rockpi GPIO
Audio out
Note: MilkV Duo S 2nd header (27-52) GPIO are 1.8V
12V/24V power supply

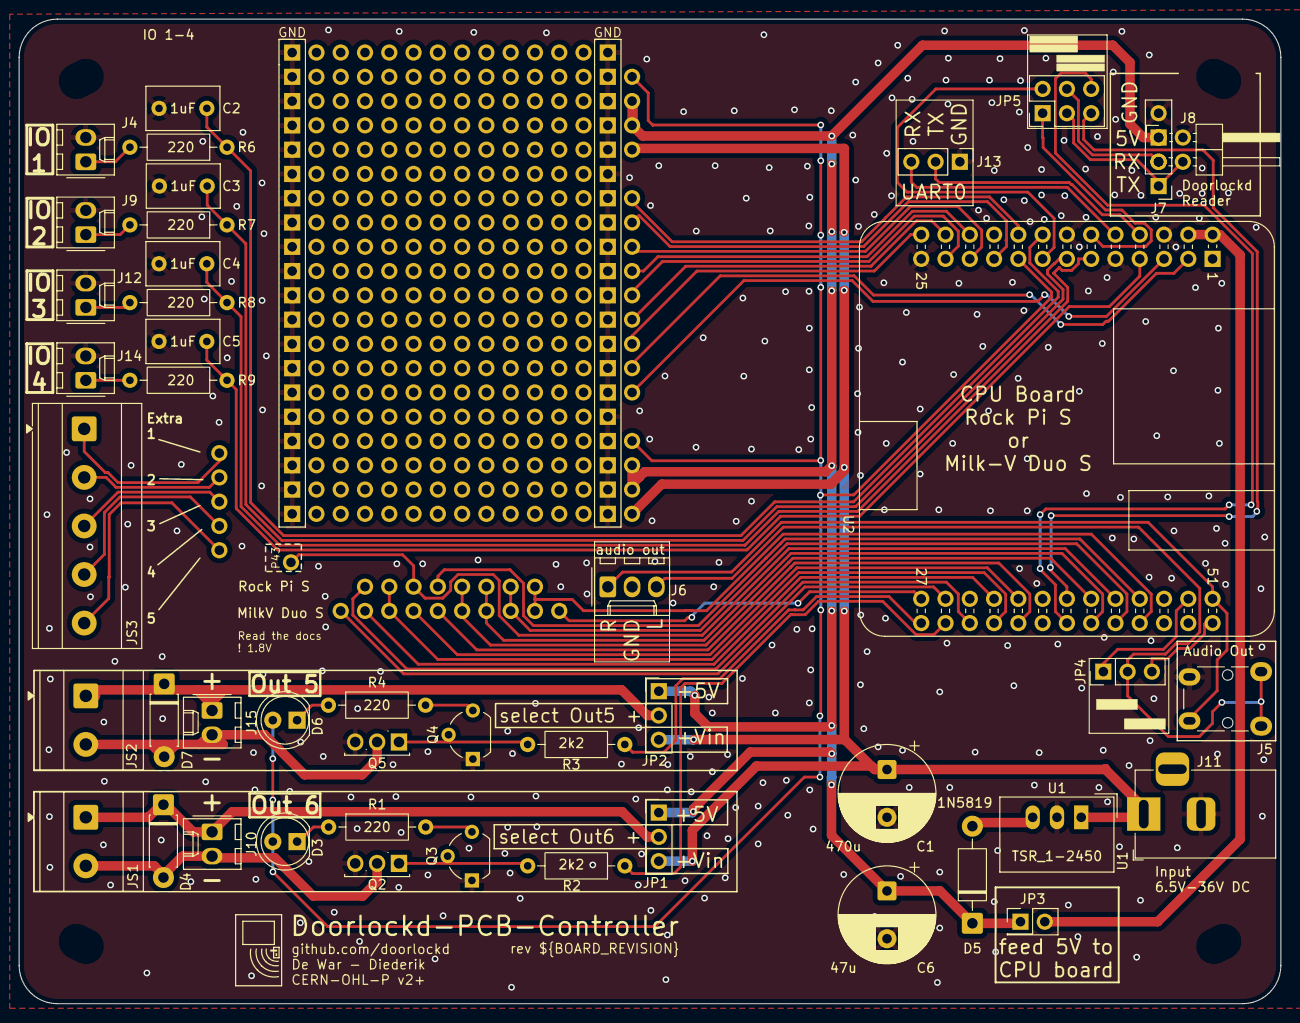
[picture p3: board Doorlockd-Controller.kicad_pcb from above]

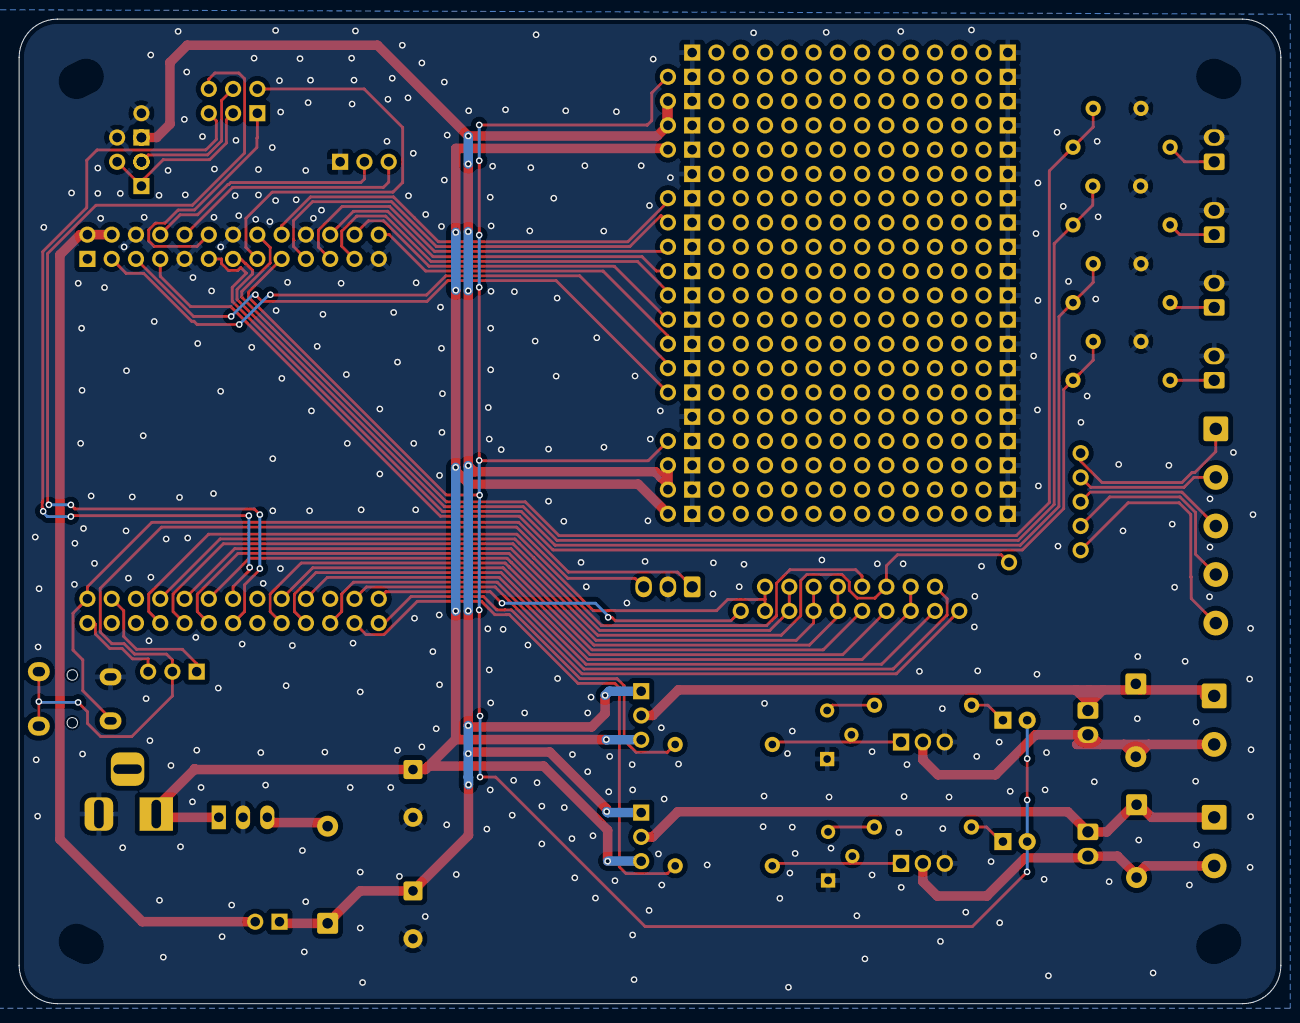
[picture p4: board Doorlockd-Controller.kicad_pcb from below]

Board: 2 copper layers, 132.0 x 103.0 mm, 59 parts (2 on the bottom side), 65 nets.

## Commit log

2025-06-17 Add initial version
    [Doorlockd-Controller.kicad_pcb, Doorlockd-Controller.kicad_sch, Milk-V Duo S and Rock Pi S Pinout.ods]
2025-06-17 Added kibot workflow for automatic versioning
    see https://github.com/matthijskooijman/PCB-workflows
    [Doorlockd-Controller.kicad_pcb, Doorlockd-Controller.kicad_sch]
2025-06-17 Fixed various ERC rule errors and warnings
    [Doorlockd-Controller.kicad_pcb, Doorlockd-Controller.kicad_sch]
2025-06-17 Fixed earlier fixed problems overwritten by last attemp to fix problems
    [Doorlockd-Controller.kicad_pcb]
2025-06-17 Adds kibot schematics pdf
2025-06-17 Adds ground plate vias
    [Doorlockd-Controller.kicad_pcb]
2025-06-18 Note audio jack actually to be used
    The 1503 07 for which we used a footprint is no longer available, but
    the 1503 30 should be pin compatible.
    [Doorlockd-Controller.kicad_pcb, Doorlockd-Controller.kicad_sch]
2025-06-18 Update footprints in schematic (from PCB)
    [Doorlockd-Controller.kicad_sch]
2025-06-18 Mark stripboard as "not in schematic"
    This prevents deleting it when updating PCB from schematic.
    [Doorlockd-Controller.kicad_pcb]
2025-06-18 Update PCB from schematic
    This imports fields (description and datasheet) for some symbols that
    were previously somehow not included.
    [Doorlockd-Controller.kicad_pcb]
2025-06-18 Fixed correct pins for ROCKPIS_UART3_RX/TX connecting PN532 Reader
    [Doorlockd-Controller.kicad_pcb, Doorlockd-Controller.kicad_sch]
2025-06-18 Fixed Pin 15 and updated the spreadsheet MILKVDUOS_UART2_RX was connected to the wrong pin14 -> pin15
    [Doorlockd-Controller.kicad_pcb, Doorlockd-Controller.kicad_sch, Milk-V Duo S and Rock Pi S Pinout.ods]
2025-06-18 Fixed Thermal relief connection to zone incomplete
    Pin 14 of Rock Pi S/MilkV Duo S by adding via to bottom layer
    Thermal relief connection to zone incomplete (layer F.Cu; 1 spokes connected to isolated island)
    [Doorlockd-Controller.kicad_pcb]
2025-06-23 Fixed readability silkscreen
    [Doorlockd-Controller.kicad_pcb]
2025-06-24 Fixed and improved spreadsheet, pcb and schema
    PCB and Schema:
    improved netlabels for PN532 related pins.
    improved netlabels for OUT_1 / OUT_2
    improved netlabels for EXP P03 / EXP P05 , and fixed copper lines accoording to silkscreen labels.
    added 3.3V pin on PCB intended for lelvel shifter Milk V DUO S (EXP_P43)
    Added help lines for mountingholes on fab layer.
    Fixed mounting holes for 120x90 & 118x91 including correct positioning.
    Spreadsheet:
    Fixed and improved color and text labels.
    [Doorlockd-Controller.kicad_pcb, Doorlockd-Controller.kicad_sch, Milk-V Duo S and Rock Pi S Pinout.ods]
2025-06-24 Fixes 3d-view for StripBoard 1x01
    [Doorlockd-Controller.kicad_pcb]
2025-06-24 Replace icon by cleaner SVG version
    [Doorlockd-Controller.kicad_pcb]
2025-06-26 Updated spreadsheets, adds StripBoard Extra Pins overview
    [Milk-V Duo S and Rock Pi S Pinout.ods, stripboard extras.ods]
2025-06-26 Cosmetic schematic changes
    [Doorlockd-Controller.kicad_sch]
2025-06-26 Cosmetic PCB changes
    [Doorlockd-Controller.kicad_pcb]
2025-06-26 Adds overview tables of all available GPIO pins
    [stripboard extras.ods]
2025-08-14 Revert "Adds kibot schematics pdf"
    This reverts commit 4520ee80d4823f830d35762883774dac6c1f55b6.
    The default config already generates a schematic, so no need for
    a custom config here.
2025-08-14 Replace STU60N3LH5 FET with STD12NF06L-1
    The former is not available anymore since a while, the latter is
    another IPAK FET with similar specs.
    [Doorlockd-Controller.kicad_pcb, Doorlockd-Controller.kicad_sch]
2025-08-14 Improve mounting hole accuracy
    Turns out these holes were actually 26.565 degrees (atan(0.5)), not 22.5.
    This fixes the footprint to angle the pad at 26.5 and puts the courtyard
    and user comments figures in the exactly correct spot.
    This also renames the footprint, switching from specifying the angle
    (which would be inexact) to the center offset of the second hole.
    [Doorlockd-Controller.kicad_pcb, Doorlockd-Controller.kicad_sch]
2025-08-14 Add PCB and mounting hole dimensions
    This also removes the text area with some of these dimensions and info
    about what housings are intended to be used. The latter will be readded
    in the README.
    [Doorlockd-Controller.kicad_pcb]
2025-08-24 Change license to CERN-OHL-P v2+
    Also makes some other small tweaks to the title sheet.
    [Doorlockd-Controller.kicad_pcb, Doorlockd-Controller.kicad_sch]
2025-08-24 Update PCB from schematic
    For some reason this changes all empty datasheets to ~.
    [Doorlockd-Controller.kicad_pcb]
2025-08-24 Refill zones and let KiCad update tables
    Somehow when opening this file in my KiCad version, it makes changes to
    table definitions in the file. Maybe this is a difference between my and
    Diederik's versions, or Linux and OSX, but well.
    [Doorlockd-Controller.kicad_pcb]
2025-08-24 Change LED resistors to 220
    This reduces LED current a bit, and reduces BOM count.
    [Doorlockd-Controller.kicad_pcb, Doorlockd-Controller.kicad_sch]
2025-08-24 Some silkscreen tweaks
    [Doorlockd-Controller.kicad_pcb]
2025-09-04 PCB-workflows: Update
    This includes the following commits:
    95c1b8c Remove echo accidentally added in the previous commit
    1c8f120 Fix compatibility on Linux again
    8a94424 Switch to blender for 3D rendering
    f3d7aa1 Add 3D render to github release body
    71275f1 Set explicit permissions in workflow file
    6077991 Improve feedback for invalidly formatted tags
2025-09-04 Use correct IPAK footprint
    This used the SIPAK footprint, but that is slightly different (and has
    no 3D model), so use the IPAK/TO-251-3 footprint instead.
    [Doorlockd-Controller.kicad_pcb, Doorlockd-Controller.kicad_sch]
2025-09-11 Improve note about audio connector
    Turns out the two mentioned connectors have the same footprint, but are
    not pin-compatible (ring and sleeve are swapped).
    [Doorlockd-Controller.kicad_pcb, Doorlockd-Controller.kicad_sch]
2025-09-11 Use MOSI/MISO instead of SDO/SDI on silk
    [Doorlockd-Controller.kicad_pcb]
2025-09-11 Swap output 5 and 6
    The were accidentally mislabeled in the silkscreen. To preserve the
    logical order on the PCB, the silk is unchanged, but the schematic is
    changed to swap them instead.
    [Doorlockd-Controller.kicad_pcb, Doorlockd-Controller.kicad_sch]
2025-09-11 Improve level shifter note in schematic
    [Doorlockd-Controller.kicad_sch]
2025-09-11 Update README and pinout spreadsheet
    [Milk-V Duo S and Rock Pi S Pinout.ods, Pinout.ods, stripboard extras.ods]
2025-09-11 made title, boardname and silk consistent
    [Doorlockd-Controller.kicad_pcb, Doorlockd-Controller.kicad_sch]
2025-09-11 Move some vias away from silk
    [Doorlockd-Controller.kicad_pcb]
2025-09-11 Remove 3D models for stripboard headers
    These models were already hidden, but when a hidden model is present
    kibot still renders solder blobs in the pads. To work around that, just
    remove the models entirely.
    [Doorlockd-Controller.kicad_pcb]
2025-09-11 Remove COMPONENTS_DATE from silkscreen
    This date is intended to reflect the component selection, which can be
    changed independent of the PCB layout, so it should not be reflected on
    the actual board.
    [Doorlockd-Controller.kicad_pcb]
2025-09-11 Fix a via position and do a zone fill
    This via was accidentally put on top of a trace, and when modifying the
    vias, a zone fill was forgotten.
    [Doorlockd-Controller.kicad_pcb]
2025-09-11 Improved logo and boardname position
    [Doorlockd-Controller.kicad_pcb]
2025-09-18 Add 3D models to Rock Pi footprint
    This just adds two pin socket models with an offset.
    [Doorlockd-Controller.kicad_pcb]
2025-09-18 Make mounting holes non-plated
    It seems that having a pad around an oval hole confuses Aisler and
    produces a weird result (at least in the preview, Aisler has not yet
    finished investigating whether there is also a problem in actual
    production).
    As a workaround, make the holes nonplated (and make the pad size equal
    to the hole size), since we do not really need the grounding currently
    (but this makes minimal changes to allow reverting this later on). This
    also sets the "zone connection" to "none", to prevent thermal spokes to
    the non-existing pad (without having to modify the schematic to not
    connect these pads to GND, which would be the proper way for a regular
    NPTH).
    [Doorlockd-Controller.kicad_pcb]
2025-09-18 Re-release v2.0
    Turns out the oval mounting holes caused an issue with Aisler, so they
    were changed to be non-plated to work around that. So this is the real
    2.0 version that will be manufactured.
2025-10-01 Swap output 5 and 6
    was already updated in kicad but not in the spreadsheet
    [Pinout.ods]

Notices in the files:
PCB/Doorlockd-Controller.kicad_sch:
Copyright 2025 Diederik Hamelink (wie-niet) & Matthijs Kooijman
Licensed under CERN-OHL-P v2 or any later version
